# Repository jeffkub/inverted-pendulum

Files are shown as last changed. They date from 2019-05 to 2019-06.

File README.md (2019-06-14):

# Inverted Pendulum 

Classic inverted pendulum control system implemented in Python.

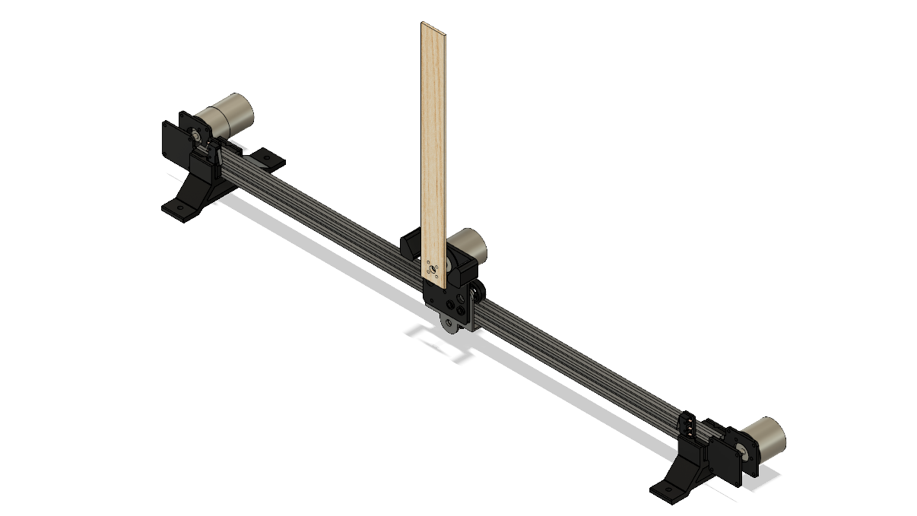
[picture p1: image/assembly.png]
Assembly


## Parts List

- [Encoder](https://www.amazon.com/gp/product/B00UTIFCVA) Qty 2
- [Motor](https://www.amazon.com/uxcell-550RPM-Electric-Reduction-Centric/dp/B01KTZXZDE)
- [Extruder Back Support Plate](https://www.amazon.com/Creality-Original-Extruder-Support-3D/dp/B07KXQPB29)
- [2020 Linear Rail 700mm](https://www.amazon.com/Iverntech-European-Standard-Anodized-Extrusion/dp/B07GRL7FHJ/)
- [GT2 Timing Belt](https://www.amazon.com/Mercurry-Meters-timing-Rostock-GT2-6mm/dp/B071K8HYB4)
- [GT2 Pulley 20 Tooth 6mm Bore](https://www.amazon.com/gp/product/B07CXR7SFL)
- [6mm Flanged Shaft Coupling](https://www.amazon.com/HJ-Garden-Coupling-Hardness-Connection/dp/B07JCQ32T6)
- [M3x20mm Standoff](https://www.amazon.com/HobbyPark-Aluminum-M3x20mm-Standoff-Female-Female/dp/B071X49WPX)
- [Rubber Feet](https://www.amazon.com/gp/product/B073WMSQ21)
- [Limit Switches](https://www.amazon.com/gp/product/B076GM7JQP/)
- Arduino UNO
- [Adafruit Motor Shield for Arduino V2](https://www.adafruit.com/product/1438)
- [Arduino Screw Terminal Shield](https://www.amazon.com/gp/product/B07HF2DD7T)
- [12V DC Power Supply](https://www.amazon.com/gp/product/B073QTNF9F)
- [12V Sealed Lead Acid Battery](https://www.amazon.com/gp/product/B00A82A4N8/)

3D printed parts can be found under the mechanical folder.

- Encoder Bracket.stl: Attaches encoder and motor to the linear rail, Qty 2
- Front Left Bracket.stl: Attaches limit switch to linear rail
- Front Right Bracket.stl: Attaches limit switch to linear rail
- Stand.stl: Support stand, slides on the brackets, Qty 2
- Pendulum Bracket.stl: Attaches pendulum + encoder to the slide

## Wiring Diagram

TODO

The 12V battery helps with motor transients. Without it, the power supply will frequently cut out when the motor changes directions.

## Arduino Programming 

TODO

## Control Program 

TODO

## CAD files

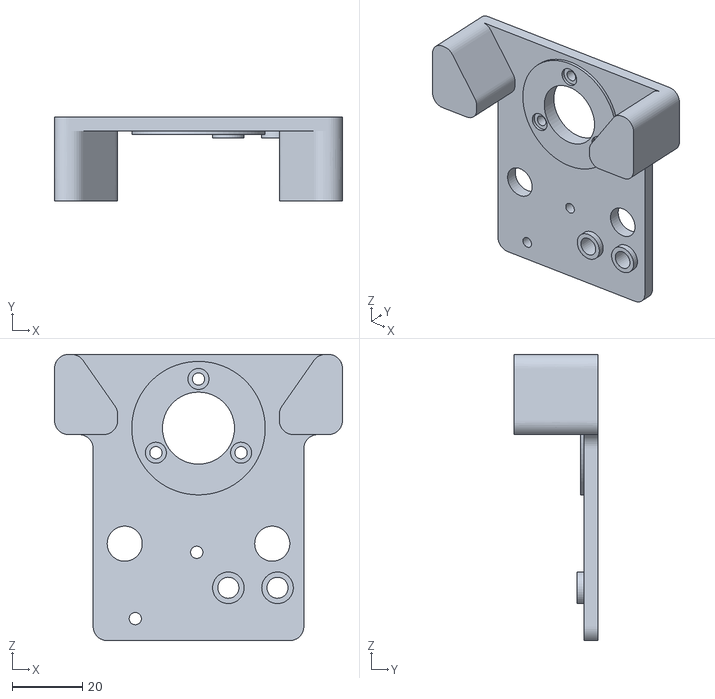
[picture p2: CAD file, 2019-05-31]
mechanical/Pendulum Bracket.stl
82.0 x 24.0 x 81.5

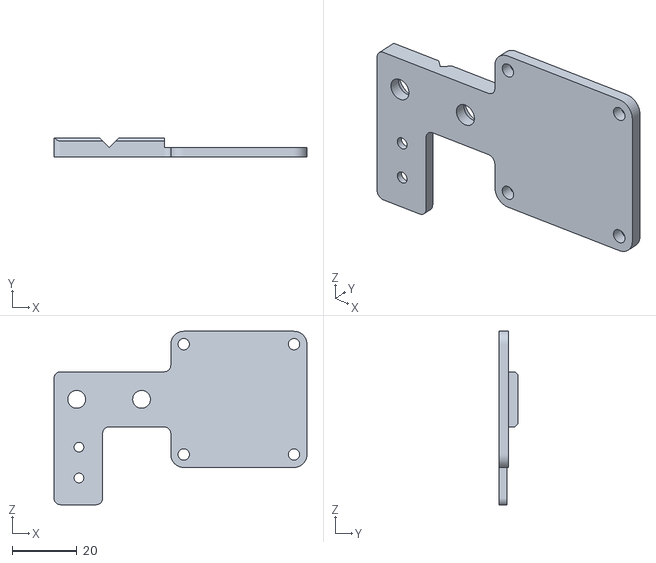
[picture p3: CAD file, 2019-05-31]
mechanical/Front Right Bracket.stl
78.0 x 6.00 x 53.5

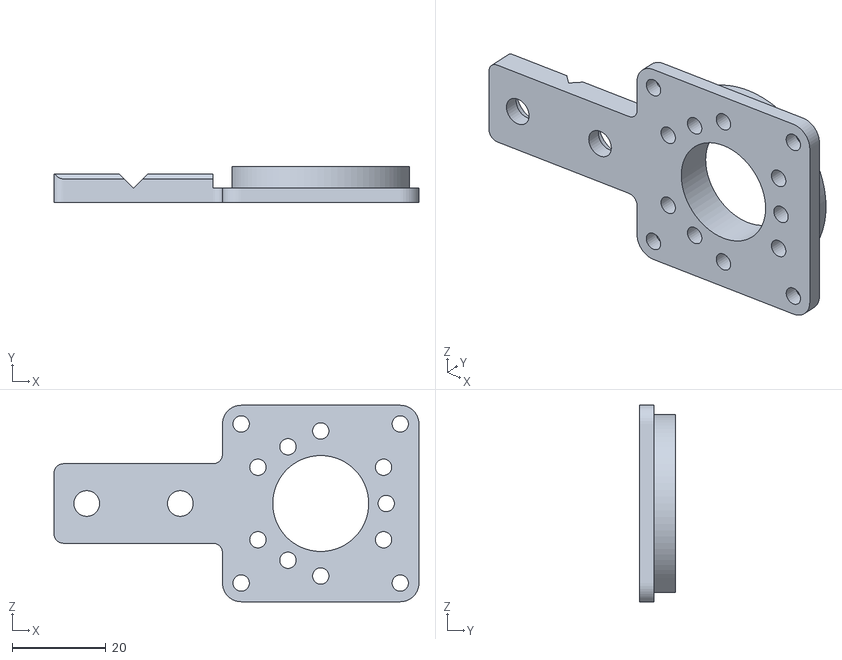
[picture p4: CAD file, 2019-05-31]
mechanical/Encoder Bracket.stl
78.0 x 7.60 x 42.0

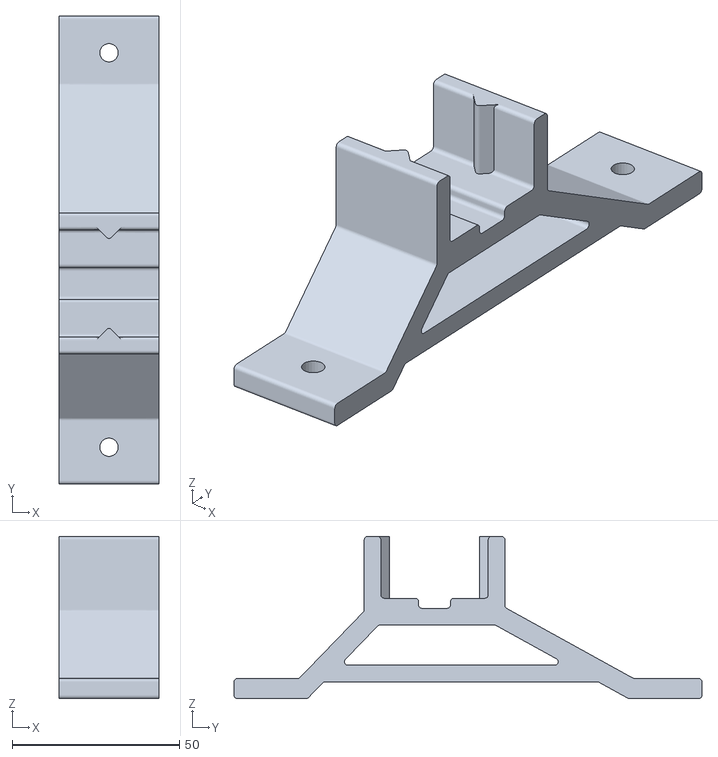
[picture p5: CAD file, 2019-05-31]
mechanical/Stand.stl
30.0 x 140.0 x 48.5

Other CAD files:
mechanical/Front Left Bracket.stl

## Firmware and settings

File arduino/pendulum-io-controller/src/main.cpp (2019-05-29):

#include <Arduino.h>

#include <Adafruit_MotorShield.h>

#define LED_PIN         LED_BUILTIN
#define ENCODER1_A_PIN  2
#define ENCODER1_B_PIN  5
#define ENCODER2_A_PIN  3
#define ENCODER2_B_PIN  4
#define LIMIT1_PIN      10
#define LIMIT2_PIN      11

#define LED_PERIOD      250
#define MOTOR_TIMEOUT   1000

#define BUF_LEN         32

static void encoder1APinChange();
static void encoder2APinChange();

static void handleBlink();

static void cmdGetInputs();
static void cmdSetMotor(long speed);
static void handleLine(const char * line);
static void handleSerial();

static void handleMotorTimeout();

static Adafruit_MotorShield motor_shield = Adafruit_MotorShield();
static Adafruit_DCMotor * motor = motor_shield.getMotor(1);

static volatile long encoder1 = 0;
static volatile long encoder2 = 0;

static unsigned long last_motor_update = 0;

static void encoder1APinChange()
{
    encoder1 += (digitalRead(ENCODER1_A_PIN) == digitalRead(ENCODER1_B_PIN)) ? +1 : -1;
}

static void encoder2APinChange()
{
    encoder2 += (digitalRead(ENCODER2_A_PIN) == digitalRead(ENCODER2_B_PIN)) ? +1 : -1;
}

static void handleBlink()
{
    static unsigned long last = 0;
    static uint8_t state = LOW;

    if(millis() - last < LED_PERIOD)
        return;

    last += LED_PERIOD;

    state = (state == LOW) ? HIGH : LOW;
    digitalWrite(LED_PIN, state);
}

static void cmdGetInputs()
{
    long encoder1_temp;
    long encoder2_temp;
    int limit1_temp;
    int limit2_temp;

    noInterrupts();
    encoder1_temp = encoder1;
    encoder2_temp = encoder2;
    interrupts();

    limit1_temp = digitalRead(LIMIT1_PIN);
    limit2_temp = digitalRead(LIMIT2_PIN);

    Serial.print(encoder1_temp);
    Serial.print("\t");
    Serial.print(encoder2_temp);
    Serial.print("\t");
    Serial.print(limit1_temp);
    Serial.print("\t");
    Serial.println(limit2_temp);
    Serial.flush();
}

static void cmdSetMotor(long speed)
{
    /* Clamp speed value */
    speed = (speed >  2047) ?  2047 : speed;
    speed = (speed < -2047) ? -2047 : speed;

    if(speed == 0)
    {
        motor->setSpeed(0);
        motor->run(RELEASE);
    }
    else if(speed > 0)
    {
        motor->setSpeed(speed << 1);
        motor->run(FORWARD);
    }
    else
    {
        motor->setSpeed((-speed) << 1);
        motor->run(BACKWARD);
    }

    last_motor_update = millis();
}

static void handleLine(const char * line)
{
    long val;

    if(strcmp(line, "R") == 0)
    {
        cmdGetInputs();
    }
    else if(sscanf(line, "M1 : %ld", &val) == 1)
    {
        cmdSetMotor(val);
    }
}

static void handleSerial()
{
    static char buf[BUF_LEN+1] = {0};
    static unsigned len = 0;
    char input;

    while(Serial.available())
    {
        input = Serial.read();

        if(len == 0 && isspace(input))
            continue;

        if(input == '\r' || input == '\n')
        {
            buf[len] = '\0';
            handleLine(buf);
            len = 0;
            break;
        }
        else if(len < BUF_LEN)
        {
            buf[len] = input;
            len++;
        }
    }
}

static void handleMotorTimeout()
{
    unsigned long cur;

    cur = millis();

    if(cur - last_motor_update >= MOTOR_TIMEOUT)
    {
        last_motor_update = cur;

        /* Disable the motor if no command has been received in a while */
        motor->setSpeed(0);
        motor->run(RELEASE);
    }
}

void setup()
{
    pinMode(LED_PIN, OUTPUT);
    pinMode(ENCODER1_A_PIN, INPUT_PULLUP);
    pinMode(ENCODER1_B_PIN, INPUT_PULLUP);
    pinMode(ENCODER2_A_PIN, INPUT_PULLUP);
    pinMode(ENCODER2_B_PIN, INPUT_PULLUP);
    pinMode(LIMIT1_PIN, INPUT_PULLUP);
    pinMode(LIMIT2_PIN, INPUT_PULLUP);

    Serial.begin(115200);

    motor_shield.begin();

    attachInterrupt(digitalPinToInterrupt(ENCODER1_A_PIN), encoder1APinChange, CHANGE);
    attachInterrupt(digitalPinToInterrupt(ENCODER2_A_PIN), encoder2APinChange, CHANGE);
}

void loop()
{
    handleBlink();
    handleSerial();
    handleMotorTimeout();
}

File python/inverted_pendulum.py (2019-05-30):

#!/usr/bin/env python3

import argparse
import json
import sys
import time
import traceback

import numpy as np

from arduino_io import ArduinoIO
from cart import Cart

class Controller:
	def __init__(self, params, sensors, motor):
		self.dt = params['dt']['val']
		self.Khat = np.array(params['Khat']['val'])

		self.cart = Cart(params, sensors, motor)

		self.r = 0.0
		self.zeta = 0.0

	def _waitForNextStep(self):
		time.sleep(max(0, self.dt - (time.time() - self.last_time)))
		self.last_time += self.dt

	def _step(self):
		# Get the current state of the cart
		[state, y] = self.cart.nextState(self.dt)

		# Zeta is the integral of the position error
		self.zeta += (self.r - y) * self.dt

		# The control equation
		u = np.dot(-self.Khat, np.append(state, self.zeta))

		self.cart.setForce(u)

	def setup(self):
		# Initialize encoder positions
		self.cart.zeroTheta()
		self.cart.findLimits()

	def run(self):
		# Center the cart
		self.cart.goTo(0.0)

		# Wait for the pendulum to be moved into position by hand
		self.cart.waitForPendulum()

		# Control loop
		self.last_time = time.time()
		self.zeta = 0.0

		self.cart.resetState()

		while True:
			self._waitForNextStep()
			self._step()

			# Make sure the cart doesn't crash into the ends
			if not self.cart.checkLimits():
				break

def main(argv):
	parser = argparse.ArgumentParser()
	parser.add_argument('--port', default='/dev/ttyACM0', help='Serial port')
	parser.add_argument('--baud', default=115200, help='Baud rate')
	parser.add_argument('--params', default='params.json', help='Parameter file')

	args = parser.parse_args(argv[1:])

	with open(args.params) as file:
		params = json.load(file)

	arduino = ArduinoIO(params, port=args.port, baud=args.baud)
	controller = Controller(params, sensors=arduino, motor=arduino)

	try:
		controller.setup()
		while True:
			controller.run()
	except:
		print(traceback.format_exc())

	# Make sure to disable the motor before exiting
	arduino.setMotorV(0)

	return 0

if __name__ == '__main__':
	sys.exit(main(sys.argv))

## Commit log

2019-05-24 Add arduino code
2019-05-27 Add motor equation, adjust cart parameters
2019-05-27 Remove motor dead zone check
2019-05-29 Improved motor starting torque algorithm. Added pendulum starting angle
2019-05-29 Add motor control timeout
2019-05-31 Create stl files for 3D printed parts
    [Encoder Bracket.stl, Front Left Bracket.stl, Front Right Bracket.stl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]
